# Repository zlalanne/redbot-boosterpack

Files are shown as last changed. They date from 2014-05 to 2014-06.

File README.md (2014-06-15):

# RedBot BoosterPack

Imgur RedBot BoosterPack

This project is a port of Sparkfun's RedBot Mainboard to BoosterPack form to be used with TI LaunchPads + Energia

Please check the GitHub issue tracker for any known hardware/software issues

## Changes from SparkFun's RedBot Mainboard
* Removed Atmega328 and replaced with BoosterPack headers. BoosterPack should work with any 40-pin launchpad that follows the [BoosterPack pinout standard](http://www.ti.com/ww/en/launchpad/img/launchpad-byob-pinout.png)
* Removed XBee to make board cheaper, if XBee needed get another BoosterPack
* Made sizes of caps/resistors larger to make soldering easier
* Most of the logic now runs on 3.3V since the F5529 is 3.3V as well
* Removed USB connection that was using for programming device, programming is handled on the LaunchPad
* Changed layout from 4 layer to 2 layer

## Additional Hardware Support
One of the great features about the RedBot ecosystem is the number of products SparkFun has come out with that plug into the RedBot. 

The following are currently fully supported:
* [Magician Chasis (including motors)](https://www.sparkfun.com/products/10825)
* [RedBot Buzzer](https://www.sparkfun.com/products/12567)
* [RedBot Sensor - Mechanical Bumper](https://www.sparkfun.com/products/11999). Need to put instructions on wiki

The following are under development
* [RedBot Sensor - Line Follower](https://www.sparkfun.com/products/11769). Needs software support
* [RedBot Sensor - Wheel Encoder](https://www.sparkfun.com/products/12617). Needs software support
* [RedBot Sensor - Accelerometer](https://www.sparkfun.com/products/12589). Issue with v1.0 of board, needs software support

## Repository Contents
* **/Firmware/RedBot** - RedBot Energia library
* **/Hardware** - Eagle PCB layout and schematic files along with BOM

## License Information
License is inherited from [SparkFun's RedBot repository](https://github.com/sparkfun/RedBot)

All contents of this repository are released under [Creative Commons Share-alike 3.0](http://creativecommons.org/licenses/by-sa/3.0/).

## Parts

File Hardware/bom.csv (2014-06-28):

Manufacturer Part Number | Digikey | Description | Price | Quantity | Total Price
PJ-102A | CP-102A-ND | Power Jack | $1.00 | 1 | $1.00
AYZ0202 | 401-2013-1-ND | Switch | $1.33 | 2 | $2.66
TB6612FNG | TB6612FNG(OC8EL)CT-ND | Motor Driver | $3.15 | 1 | $3.15
MIC5219-5.0YM5 TR | 576-2770-1-ND | LDO | $2.01 | 1 | $2.01
IRF7509TRPBF | IRF7509TRPBFCT-ND | FET Array | $0.84 | 1 | $0.84
LTST-C150GKT | 160-1169-1-ND | Green Power LED | $0.34 | 1 | $0.34
RC1206JR-0710KL | 311-10KERCT-ND | 10k resistors | $0.10 | 3 | $0.30
RC1206FR-071KL | 311-1.00KFRCT-ND | 1k resistors | $0.10 | 1 | $0.10
C1206C104K5RACTU | 399-1249-1-ND | 0.1uF Caps | $0.07 | 2 | $0.15
T491A106K010AT | 399-3684-1-ND | 10uF Caps | $0.34 | 2 | $0.67
MBRA140T3G | MBRA140T3GOSCT-ND | Schottky Diode | $0.33 | 1 | $0.33
SSW-103-22-G-P-RA-LL |  | Right angle headers for motors |  | 2
Total |  |  |  |  | $11.55

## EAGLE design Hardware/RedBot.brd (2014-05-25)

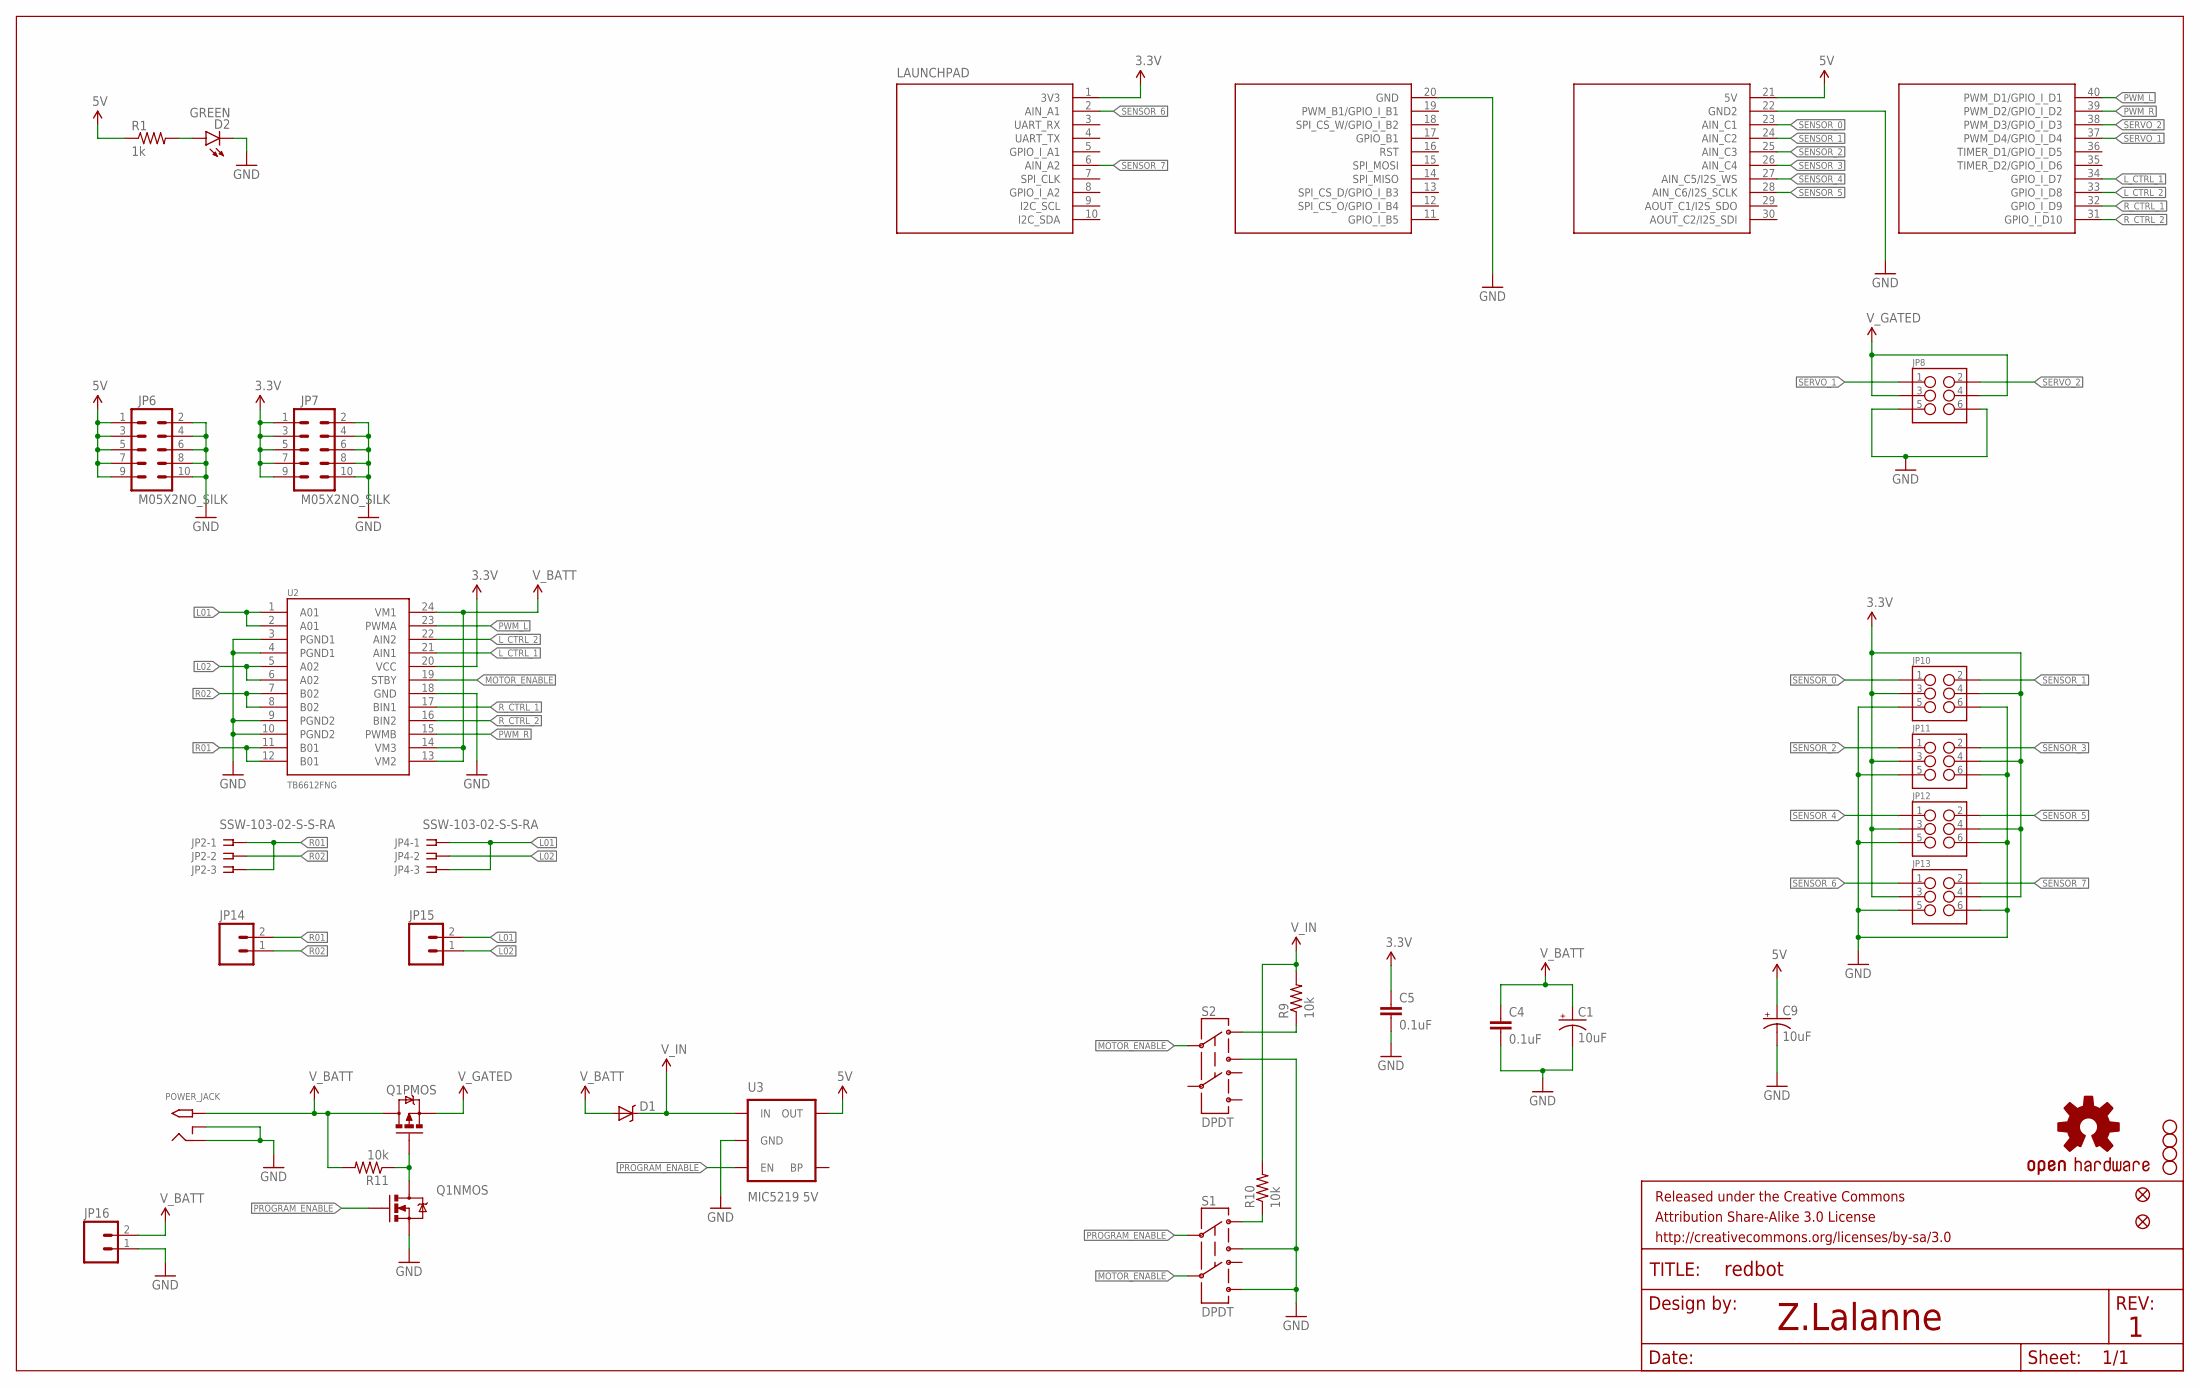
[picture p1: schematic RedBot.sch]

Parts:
C1, C9: 10uF; EIA3216
C4, C5: 0.1uF; 1206
D1: B340A; SMA-DIODE
D2: GREEN; LED-1206
FID1, FID2: FIDUCIALUFIDUCIAL; MICRO-FIDUCIAL
FRAME1: FRAME-LETTER; CREATIVE_COMMONS
JP2, JP4: SSW-103-02-S-S-RA
JP6, JP7: M05X2NO_SILK; 2X5_NOSILK
JP8, JP10, JP11, JP12, JP13: M03X22X3_SILK_SM; 2X3
JP14, JP15, JP16: M02PTH; 1X02
LAUNCHPAD: BOOSTERPACK; BOOSTERPACK40
POWER_JACK: 2.1MMJACKTHM; PJ-102A
Q1: IRF7509; MSOP8
R1: 1k; 1206
R9, R10, R11: 10k; 1206
S1, S2: DPDT; AYZ0202
STANDOFF1, STANDOFF2, STANDOFF3, STANDOFF4: STAND-OFF
U2: TB6612FNG; SSOP24
U3: MIC5219 5V; SOT23-5
U$17: OSHW-LOGOS; OSHW-LOGO-S

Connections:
3.3V: C5.1, JP7.1, JP7.3, JP7.5, JP7.7, JP7.9, JP10.3, JP10.4, JP11.3, JP11.4, JP12.3, JP12.4, JP13.3, JP13.4, LAUNCHPAD.1 (3V3), U2.20 (VCC)
5V: C9.A (+), JP6.1, JP6.3, JP6.5, JP6.7, JP6.9, LAUNCHPAD.21 (5V), R1.1, U3.5 (OUT)
GND: C1.C (-), C4.2, C5.2, C9.C (-), D2.C, JP6.2, JP6.4, JP6.6, JP6.8, JP6.10, JP7.2, JP7.4, JP7.6, JP7.8, JP7.10, JP8.5, JP8.6, JP10.5, JP10.6, JP11.5, JP11.6, JP12.5, JP12.6, JP13.5, JP13.6, JP16.1, LAUNCHPAD.20 (GND), LAUNCHPAD.22 (GND2), POWER_JACK.RING, POWER_JACK.RING_SW, Q1.1 (S), S1.3, S1.6, S2.3, U2.3 (PGND1), U2.4 (PGND1), U2.9 (PGND2), U2.10 (PGND2), U2.18 (GND), U3.2 (GND)
L01: JP4.1, JP4.3, JP15.2, U2.1 (A01), U2.2 (A01)
L02: JP4.2, JP15.1, U2.5 (A02), U2.6 (A02)
L_CTRL_1: LAUNCHPAD.34 (GPIO_I_D7), U2.21 (AIN1)
L_CTRL_2: LAUNCHPAD.33 (GPIO_I_D8), U2.22 (AIN2)
MOTOR_ENABLE: S1.5, S2.2, U2.19 (STBY)
unnamed: D2.A, R1.2
unnamed: Q1.4 (G), Q1.7 (D), Q1.8 (D), R11.1
unnamed: R9.1, S2.1
PG_EN: R10.1, S1.1
PROGRAM_ENABLE: Q1.2 (G), S1.2, U3.3 (EN)
PWM_L: LAUNCHPAD.40 (PWM_D1/GPIO_I_D1), U2.23 (PWMA)
PWM_R: LAUNCHPAD.39 (PWM_D2/GPIO_I_D2), U2.15 (PWMB)
R01: JP2.1, JP2.3, JP14.2, U2.11 (B01), U2.12 (B01)
R02: JP2.2, JP14.1, U2.7 (B02), U2.8 (B02)
R_CTRL_1: LAUNCHPAD.32 (GPIO_I_D9), U2.17 (BIN1)
R_CTRL_2: LAUNCHPAD.31 (GPIO_I_D10), U2.16 (BIN2)
SENSOR_0: JP10.1, LAUNCHPAD.23 (AIN_C1)
SENSOR_1: JP10.2, LAUNCHPAD.24 (AIN_C2)
SENSOR_2: JP11.1, LAUNCHPAD.25 (AIN_C3)
SENSOR_3: JP11.2, LAUNCHPAD.26 (AIN_C4)
SENSOR_4: JP12.1, LAUNCHPAD.27 (AIN_C5/I2S_WS)
SENSOR_5: JP12.2, LAUNCHPAD.28 (AIN_C6/I2S_SCLK)
SENSOR_6: JP13.1, LAUNCHPAD.2 (AIN_A1)
SENSOR_7: JP13.2, LAUNCHPAD.6 (AIN_A2)
SERVO_1: JP8.1, LAUNCHPAD.37 (PWM_D4/GPIO_I_D4)
SERVO_2: JP8.2, LAUNCHPAD.38 (PWM_D3/GPIO_I_D3)
V_BATT: C1.A (+), C4.1, D1.A, JP16.2, POWER_JACK.TIP, Q1.5 (D), Q1.6 (D), R11.2, U2.13 (VM2), U2.14 (VM3), U2.24 (VM1)
V_GATED: JP8.3, JP8.4, Q1.3 (S)
V_IN: D1.C, R9.2, R10.2, U3.1 (IN)

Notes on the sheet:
Z.Lalanne

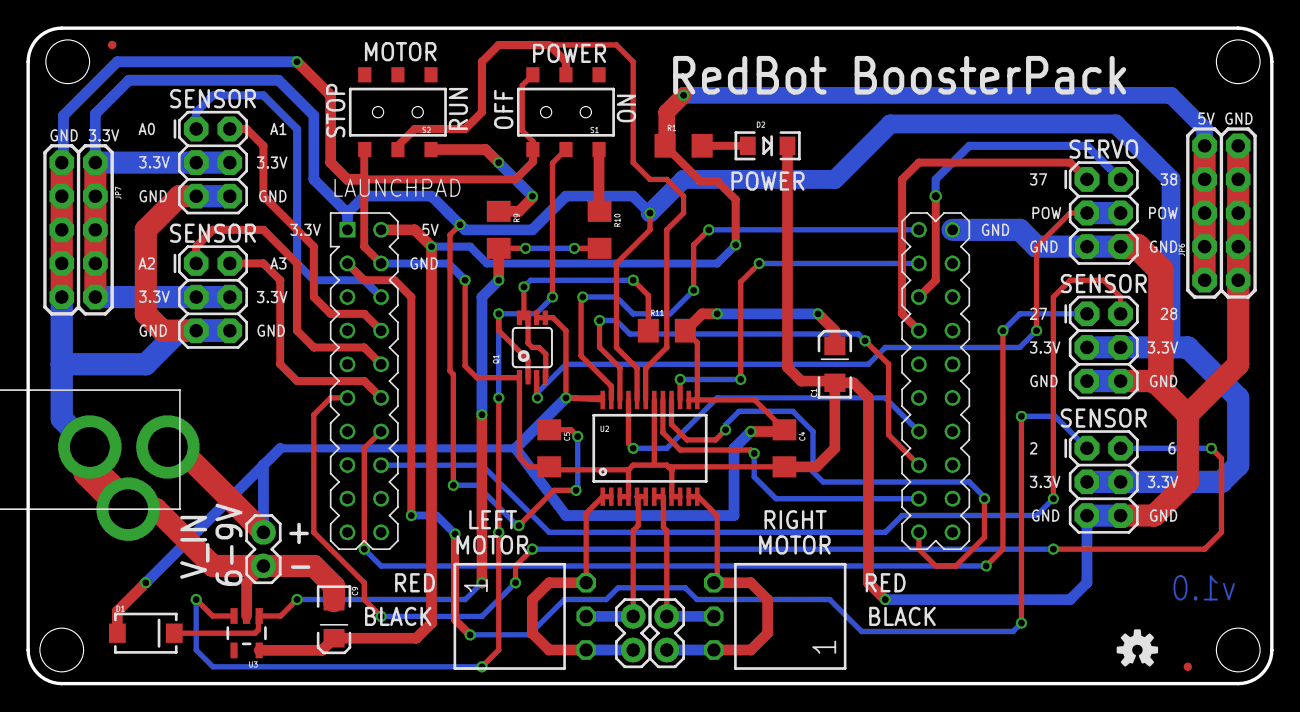
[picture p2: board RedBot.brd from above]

Board: 2 copper layers, 94.0 x 49.5 mm, 37 parts (0 on the bottom side), 32 nets.

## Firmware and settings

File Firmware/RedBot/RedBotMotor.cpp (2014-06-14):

/****************************************************************
Main CPP for RedBot motor control.

This code is beerware; if you use it, please buy me (or any other
SparkFun employee) a cold beverage next time you run into one of
us at the local.

21 Jan 2014- Mike Hord, SparkFun Electronics

Code developed in Arduino 1.0.5, on an SparkFun Redbot v12.
****************************************************************/
/****************************************************************
Migrated to Energia by Zack Lalanne
****************************************************************/

#include "RedBot.h"
#include <Energia.h>

// Constructor. Mostly for pin setup; note that it's not necessary to configure
//  PWM pins as they will be automatically configured with the analogWrite()
//  function is called.
RedBotMotor::RedBotMotor()
{
  // The interface to the motor driver is kind of ugly. It's three pins per
  //  channel: two that define role (forward, reverse, stop, brake) and one
  //  PWM input for speed.
  pinMode(R_CTRL_1, OUTPUT);
  pinMode(R_CTRL_2, OUTPUT);
  pinMode(L_CTRL_1, OUTPUT);
  pinMode(L_CTRL_2, OUTPUT);
}

// stop() allows the motors to coast to a halt, rather than trying to stop them
//  quickly. As will be the case with functions affecting both motors, the
//  global stop just calls the individual stop functions for each wheel.
void RedBotMotor::stop()
{
  leftStop();
  rightStop(); 
}

// brake() effectively shorts the two leads of the motor together, which causes
//  the motor to resist being turned. It stops quite quickly. 
void RedBotMotor::brake()
{
  leftBrake();
  rightBrake(); 
}

// drive() starts both motors. It figures out whether the motors should go
//  forward or revers, then calls the appropriate individual functions. Note
//  the use of a 16-bit integer for the speed input; an 8-bit integer doesn't
//  have the range to reach full speed. The calls to the actual drive functions
//  are only 8-bit, since we only have 8-bit PWM.
void RedBotMotor::drive(int speed)
{
  if (speed > 0)
  {
    leftFwd((byte)(abs(speed)));
    rightFwd((byte)(abs(speed)));
  }
  else
  {
    leftRev((byte)(abs(speed)));
    rightRev((byte)(abs(speed)));
  }
}

// pivot() is very much like drive(), except the motors are driven in opposite
//  directions, so as to pivot the motor on it's central axis. Positive numbers
//  are anti-clockwise rotation (assuming the motors are hooked up properly).
void RedBotMotor::pivot(int speed)
{
  if (speed > 0)
  {
    leftRev((byte)(abs(speed)));
    rightFwd((byte)(abs(speed)));
  }
  else
  {
    leftFwd((byte)(abs(speed)));
    rightRev((byte)(abs(speed)));
  }
}

// Basically the same as drive, but omitting the left motor.
void RedBotMotor::rightDrive(int speed)
{
  if (speed > 0)
  {
    rightFwd((byte)(abs(speed)));
  }
  else
  {
    rightRev((byte)(abs(speed)));
  }
}

// Basically the same as drive(), but omitting the right motor.
void RedBotMotor::leftDrive(int speed)
{
  if (speed > 0)
  {
    leftFwd((byte)(abs(speed)));
  }
  else
  {
    leftRev((byte)(abs(speed)));
  }
}

// From here out, we deal with the nitty gritty details of telling the motor
//  driver what to do. For more information about this, refer to the TB6612FNG
//  datasheet.
void RedBotMotor::leftBrake()
{
  digitalWrite(L_CTRL_1, HIGH);
  digitalWrite(L_CTRL_2, HIGH);
  analogWrite(PWM_L, 0);
}

void RedBotMotor::rightBrake()
{
  digitalWrite(R_CTRL_1, HIGH);
  digitalWrite(R_CTRL_2, HIGH);
  analogWrite(PWM_R, 0);
}

void RedBotMotor::leftStop()
{
  digitalWrite(L_CTRL_1, LOW);
  digitalWrite(L_CTRL_2, LOW);
  analogWrite(PWM_L, 0);
}

void RedBotMotor::rightStop()
{
  digitalWrite(R_CTRL_1, LOW);
  digitalWrite(R_CTRL_2, LOW);
  analogWrite(PWM_R, 0);
}

/******************************************************************************
Private functions for RedBotMotor
******************************************************************************/
// These are the motor-driver level abstractions for turning a given motor the
//  right direction. Users never see them, and *should* never see them, so we
//  make them private.

void RedBotMotor::leftFwd(byte spd)
{
  digitalWrite(L_CTRL_1, HIGH);
  digitalWrite(L_CTRL_2, LOW);
  analogWrite(PWM_L, spd);
}

void RedBotMotor::leftRev(byte spd)
{
  digitalWrite(L_CTRL_1, LOW);
  digitalWrite(L_CTRL_2, HIGH);
  analogWrite(PWM_L, spd);
}

void RedBotMotor::rightFwd(byte spd)
{
  digitalWrite(R_CTRL_1, HIGH);
  digitalWrite(R_CTRL_2, LOW);
  analogWrite(PWM_R, spd);
}

void RedBotMotor::rightRev(byte spd)
{
  digitalWrite(R_CTRL_1, LOW);
  digitalWrite(R_CTRL_2, HIGH);
  analogWrite(PWM_R, spd);
}

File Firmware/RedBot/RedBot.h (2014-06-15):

/****************************************************************
Core header file for all the various RedBot functions.

There is additional license info below regarding the use of the
SoftwareSerial library from Arduino 1.0.5; I had good and sound
reasons for creating a derivative class rather than asking users
to simply use the existing library, which are documented below.

This code is beerware; if you use it, please buy me (or any other
SparkFun employee) a cold beverage next time you run into one of
us at the local.

21 Jan 2014- Mike Hord, SparkFun Electronics

Code developed in Arduino 1.0.5, on an SparkFun Redbot v12.
****************************************************************/
/****************************************************************
Migrated to Energia by Zack Lalanne
****************************************************************/

#ifndef RedBot_h
#define RedBot_h

#include <Energia.h>

// Pin aliases for the motor controller.
#define    L_CTRL_1   34
#define    L_CTRL_2   33
#define    PWM_L      40

#define    R_CTRL_1   32
#define    R_CTRL_2   31
#define    PWM_R      39

// PCINT functionality aliases. Each PCINT has a value set up when the
//  class member gets created, and the PCINT service routine will handle
//  the choosing the appropriate response to the interrupt.
#define NOT_IN_USE    0
#define WHISKER       1
#define LENCODER      2
#define RENCODER      3
#define SW_SERIAL     4

#define PCINT_A0      0
#define PCINT_A1      1
#define PCINT_A2      2
#define PCINT_A3      3
#define PCINT_A4      4
#define PCINT_A5      5
#define PCINT_3       6
#define PCINT_9       7
#define PCINT_10      8
#define PCINT_11      9

enum WHEEL {LEFT, RIGHT, BOTH}; // Variable for which wheel you're interested in
                  //  when you do things in the encoder class.

// These three functions need to work from within multiple classes, so we keep
//  them separate and add them as friend functions where appropriate.
void setPinChangeInterrupt(int pin, byte role); // The "role" of each pin is
                  //  stored in an array which is accessed in the interrupt
                  //  handler to determine what should be done on a falling edge
                  //  PC interrupt.
void pinFunctionHandler(byte pinIndex); // This is the function which actually
                  //  handles the legwork after the interrupt has identified
                  //  which pin caught the interrupt.
void brake(void); // Globally accessible motor brake. I couldn't figure out how
                  //  to set a function pointer to the RedBotMotor class
                  //  function, and it's a small function, so I just made a
                  //  global in the library.
void PC0Handler(byte PBTemp);
void PC1Handler(byte PCTemp);
void PC2Handler(byte PDTemp);


// This class handles motor functionality. I expect one instance of this at the
//  start of a piece of RedBot code.
class RedBotMotor
{
  public:
    RedBotMotor();          // Constructor. Mainly sets up pins.
    void drive(int speed);  // Drive in direction given by sign, at speed given
                            //  by magnitude of the parameter.
    void pivot(int speed);  // Pivot more or less in place. Turns motors in
                            //  opposite directions. Positive values correspond
                            //  to anti-clockwise rotation.
    void rightDrive(int speed); // Drive just the left motor, as drive().
    void leftDrive(int speed);  // Drive just the right motor, as drive().
    void stop();            // Stop motors, but allow them to coast to a halt.
    void brake();           // Quick-stop the motors, shorting the leads.
    void rightStop();       // Stop right motor, as with stop().
    void leftStop();        // Stop left motor, as with stop().
    void leftBrake();       // Quick-stop left motor, as with brake().
    void rightBrake();      // Quick-stop right motor, as with brake().
  private:
    void leftFwd(byte speed); // These functions are pretty self-explanatory,
    void leftRev(byte speed); //  and are called by the above functions once
    void rightFwd(byte speed);//  sign has been used to determine direction.
    void rightRev(byte speed);
};

// This handles the physical wire-whisker type bumper.
class RedBotBumper
{
  public:
    RedBotBumper(int pin); // Simple constructor; when the bumper gets hit, the
                           //  motors will stop.
    RedBotBumper(int pin, void(*functionPointer)(void)); // If the user wishes
                           //  to do something other than stop on a whisker,
                           //  bump, they can write a function to do so, and
                           //  use this constructor.
    int pressed();        // Check if bumper is pressed
  private:
    int pin;
    void setBumpFunction(int pin, void(*functionPointer)(void));
};


#endif

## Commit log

2014-03-20 Initial import of redbot schematic/board
    [RedBot.brd, RedBot.sch]
2014-03-25 First pass at converting schematic
    [RedBot.brd, RedBot.sch]
2014-03-25 Updated motor ic to use 3.3V
    [RedBot.brd, RedBot.sch]
2014-03-26 Updated parts to use through hole for sensor/servo connectors
    [RedBot.brd, RedBot.sch]
2014-05-06 Updated board and schematic
2014-05-21 Updated board with new power jack. Started routing. Added BOM
    [BOM.ods, RedBot.brd, RedBot.sch]
2014-05-23 Updated all parts to be larger
    [BOM.ods, RedBot.brd, RedBot.sch]
2014-05-23 Finished layout of RedBot
    [RedBot.brd, RedBot.sch]
2014-05-25 Finished silk on board
    [RedBot.brd]
2014-05-29 Added bom in csv format
    [bom.csv]
2014-05-29 Removed old bom
    [BOM.ods]
2014-06-14 Working motors in Energia
2014-06-28 Added motor headers to BOM
    [bom.csv]
2014-10-10 PlatformIO Library Manager manifest file
    PlatformIO Library Manager manifest file
    * This library in Web: http://platformio.ikravets.com/#!/lib/show/Energia-RedBot
    * Specification: [PlatformIO Library Manager](http://docs.platformio.ikravets.com/en/latest/librarymanager/index.html)
    * Integration: [IDE Integration](http://docs.platformio.ikravets.com/en/latest/ide.html)
    `library.json` is a library manifest file which can be used with different tools/managers to organise embedded libraries. Currently, only [PlatformIO](http://platformio.ikravets.com) uses it. How doe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
    ```bash
    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

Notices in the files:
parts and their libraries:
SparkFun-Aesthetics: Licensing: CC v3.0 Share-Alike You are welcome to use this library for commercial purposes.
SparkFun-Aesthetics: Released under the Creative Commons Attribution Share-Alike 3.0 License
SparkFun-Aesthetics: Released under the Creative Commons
